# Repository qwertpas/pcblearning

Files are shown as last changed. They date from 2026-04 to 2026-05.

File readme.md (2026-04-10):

# pcblearning
A collection of PCB and firmware projects for learning PCB design. Projects are designed to have few components, cheap, yet rich in potential features.

## Using common libraries
1. After creating a new project in KiCad, copy the contents of `copy-into-your-project` into the same folder that contains your project's `.kicad_pcb` file.
2. Restart KiCad. When you place new components in the schematic or PCB editor, the `pcblearning` library should be available.

## minrc1
Tiny wheeled robot with two PM08 stepper motors, three microphones, and a buzzer. ESP32S3 supermini dev board allows for wireless control, USB-C battery charging, and running small neural networks. Microphones and buzzer may be useful for locating other robots, echolocation, and detecting surface properties (through vibration/noise from ground contact).
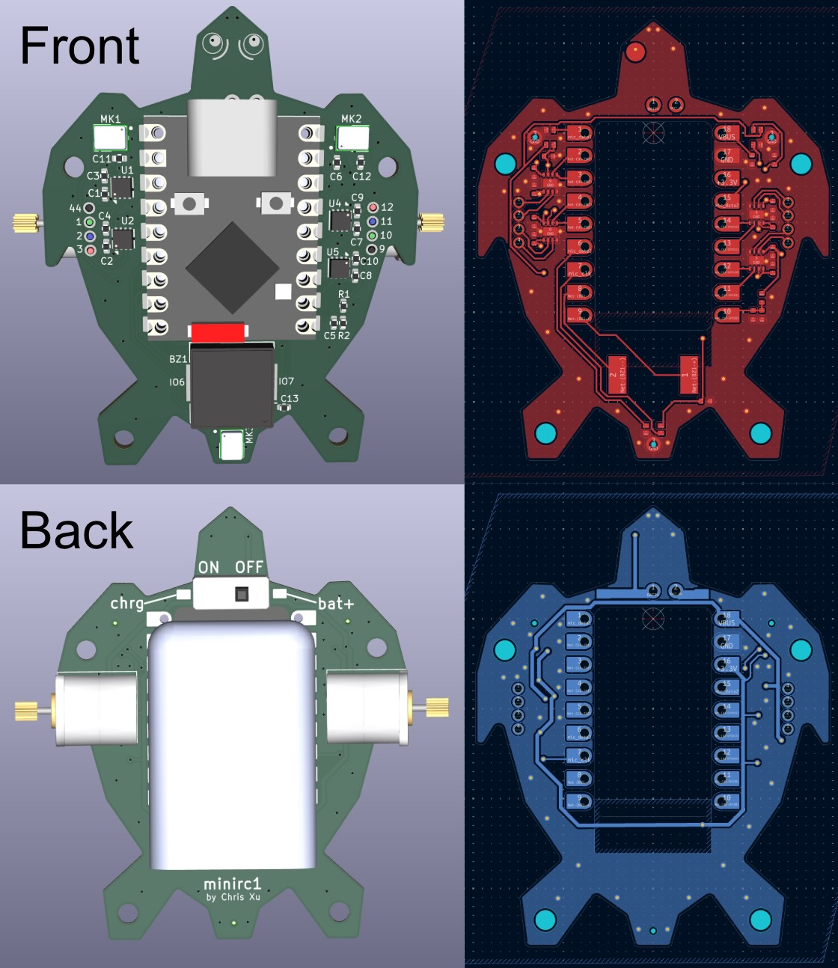
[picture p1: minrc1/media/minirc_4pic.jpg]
minrc1

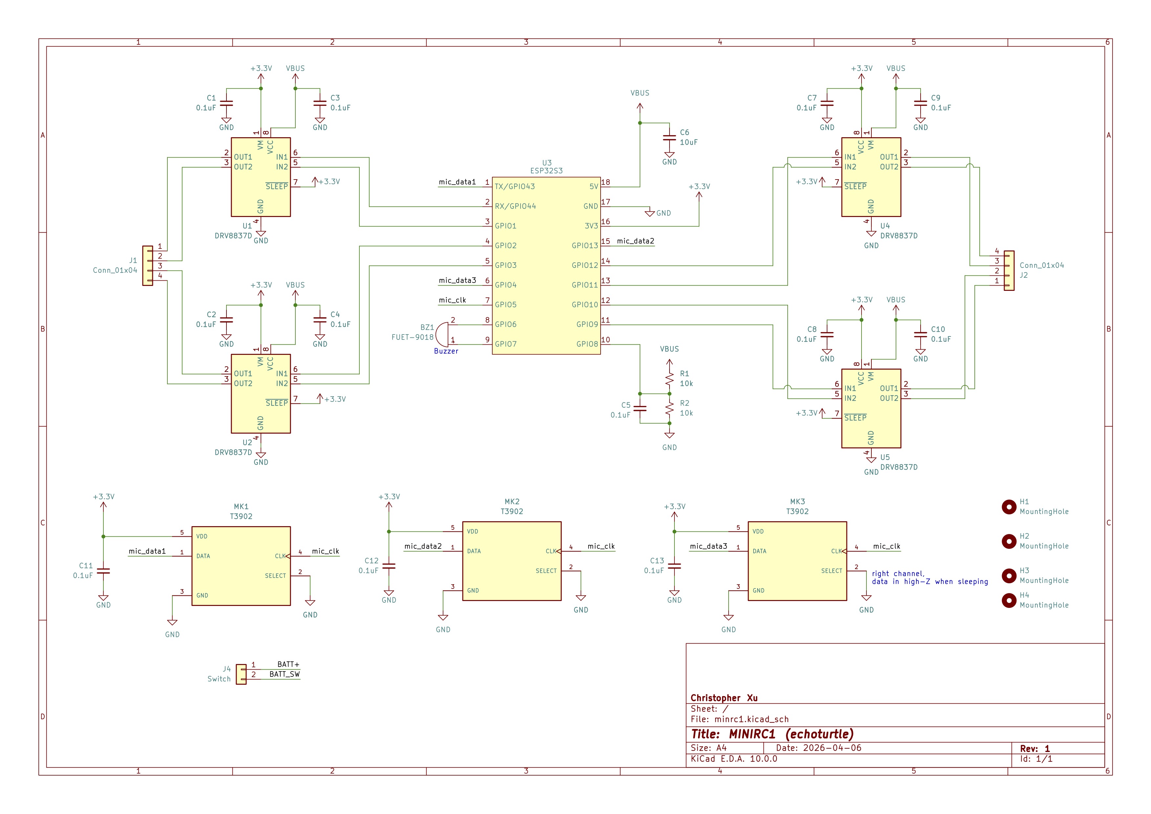
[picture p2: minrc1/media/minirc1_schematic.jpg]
schematic


## minrc-ref
Even more minimal than minrc1: just an ESP32S3-supermini, 4x DRV8837 motor drivers, 2x stepper motors, and resistor divider voltage sense. Intended as a reference design to be used as a starting point.

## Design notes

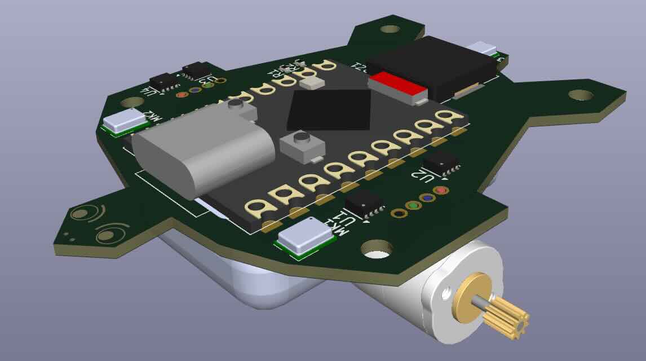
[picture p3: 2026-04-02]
minrc1/media/turtleside.jpg

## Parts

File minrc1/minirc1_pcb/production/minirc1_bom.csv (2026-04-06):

Designator | Footprint | Quantity | Value | LCSC Part #
BZ1 | Buzzer_CUI_CPT-9019S-SMT | 1 | FUET-9018
C1, C10, C11, C12, C13, C2, C3, C4, C5, C7, C8, C9 | 0402 | 12 | 0.1uF
C6 | 0402 | 1 | 10uF
J1, J2 | microstepper | 2 | Conn_01x04
J4 | PinHeader_1x02_P2.54mm_Vertical | 1 | Switch
MK1, MK2, MK3 | MIC_T3902 | 3 | T3902
R1, R2 | 0402 | 2 | 10k
U1, U2, U4, U5 | WSON-8-1EP_2x2mm_P0.5mm_EP0.9x1.6mm | 4 | DRV8837D | C39159
U3 | esp32s3-supermini | 1 | ESP32S3

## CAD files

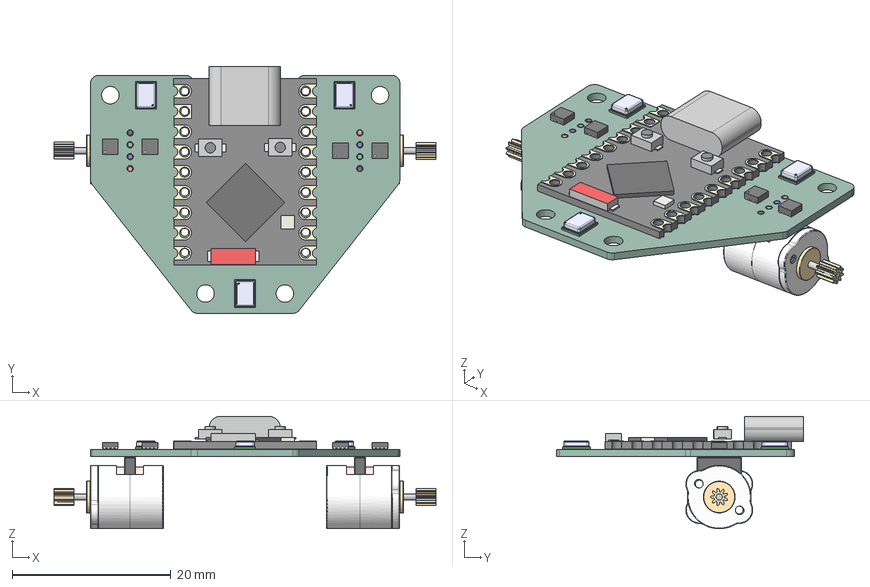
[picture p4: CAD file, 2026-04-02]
minrc1/minirc1_pcb/minirc1.step
48.2 x 31.1 x 14.2 mm
PCB
USB Type-C
SoC
BOOT
RESET
Antenna
LED
T3902 x 3
WSON-8-1EP_2x2mm_P0.5mm_EP0.9x1.6mm x 4
Spur Gear (9 teeth) x 2
Electrical Connector x 2
minrc1_PCB

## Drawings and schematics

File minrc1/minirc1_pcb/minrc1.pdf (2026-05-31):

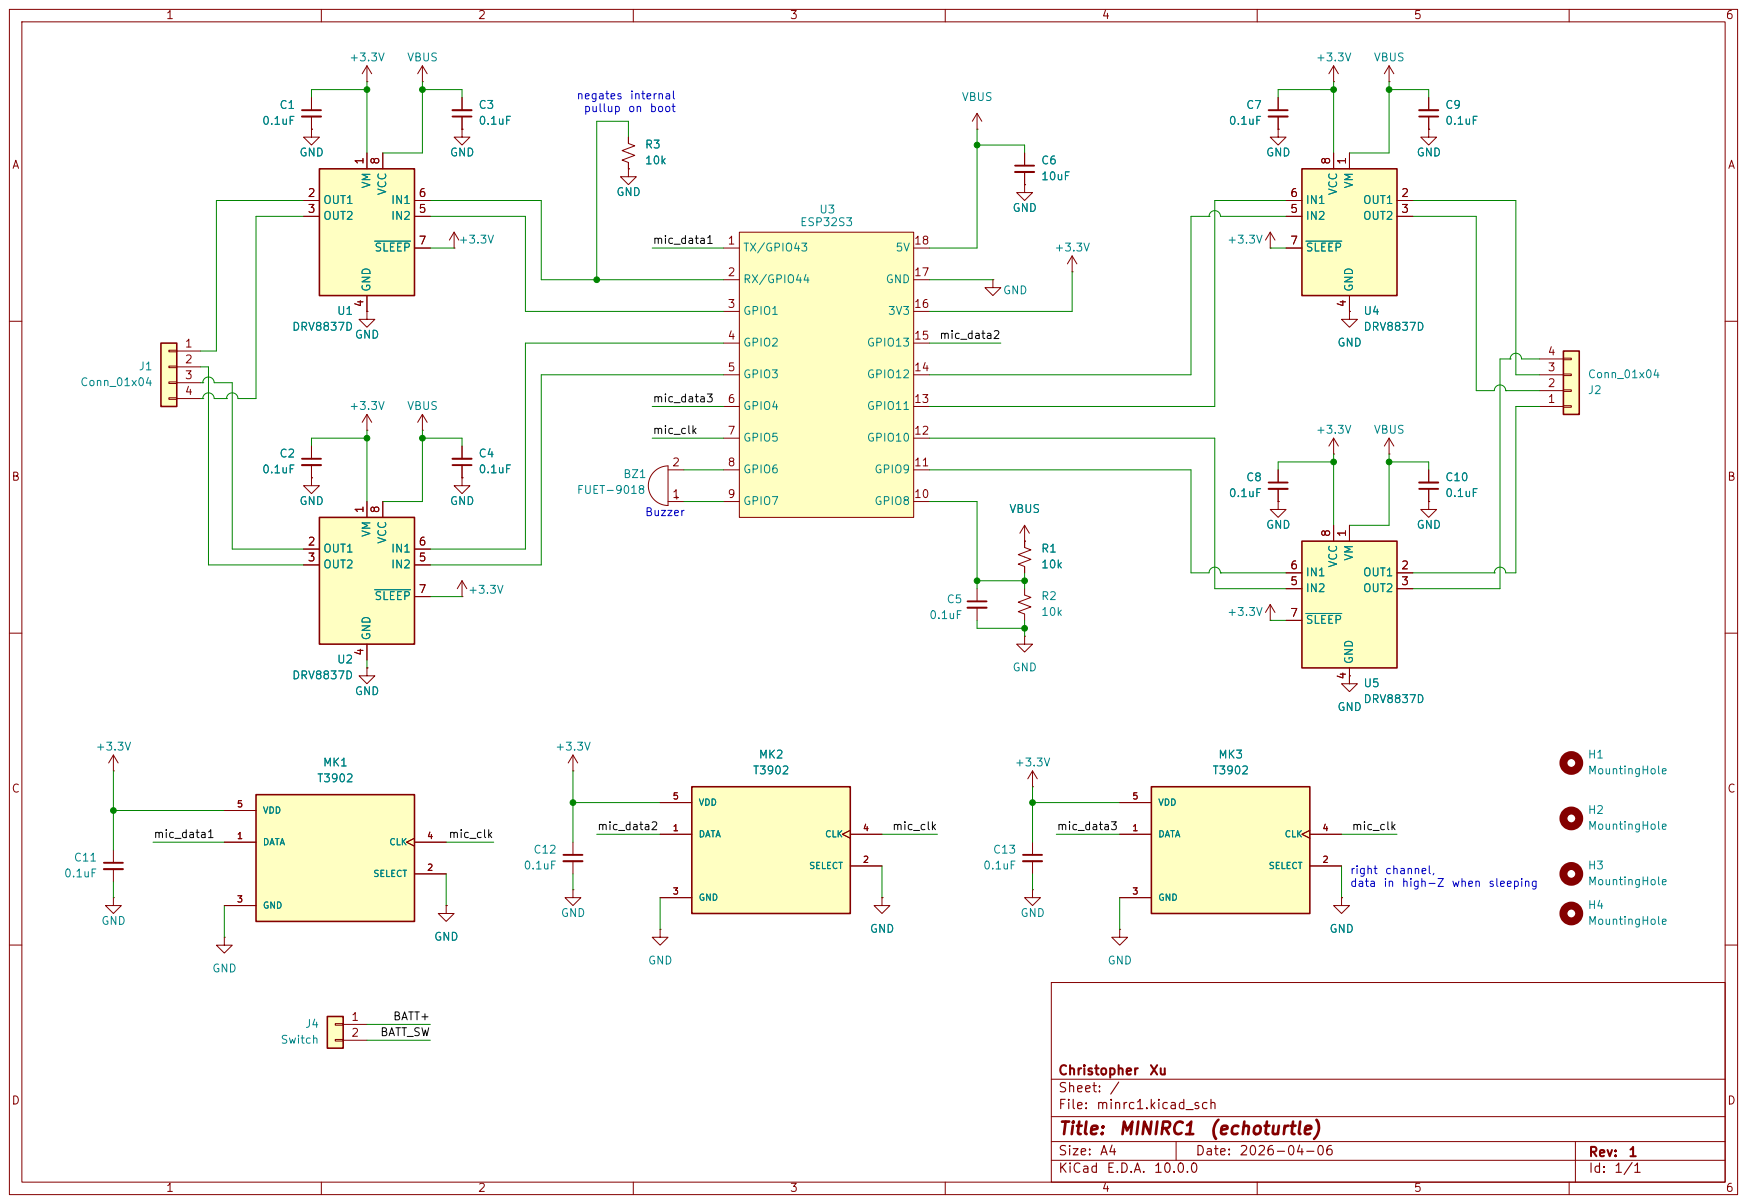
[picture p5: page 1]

right channel, data in high-Z when sleeping Buzzer negates internal

Size: A4 | Rev: 1

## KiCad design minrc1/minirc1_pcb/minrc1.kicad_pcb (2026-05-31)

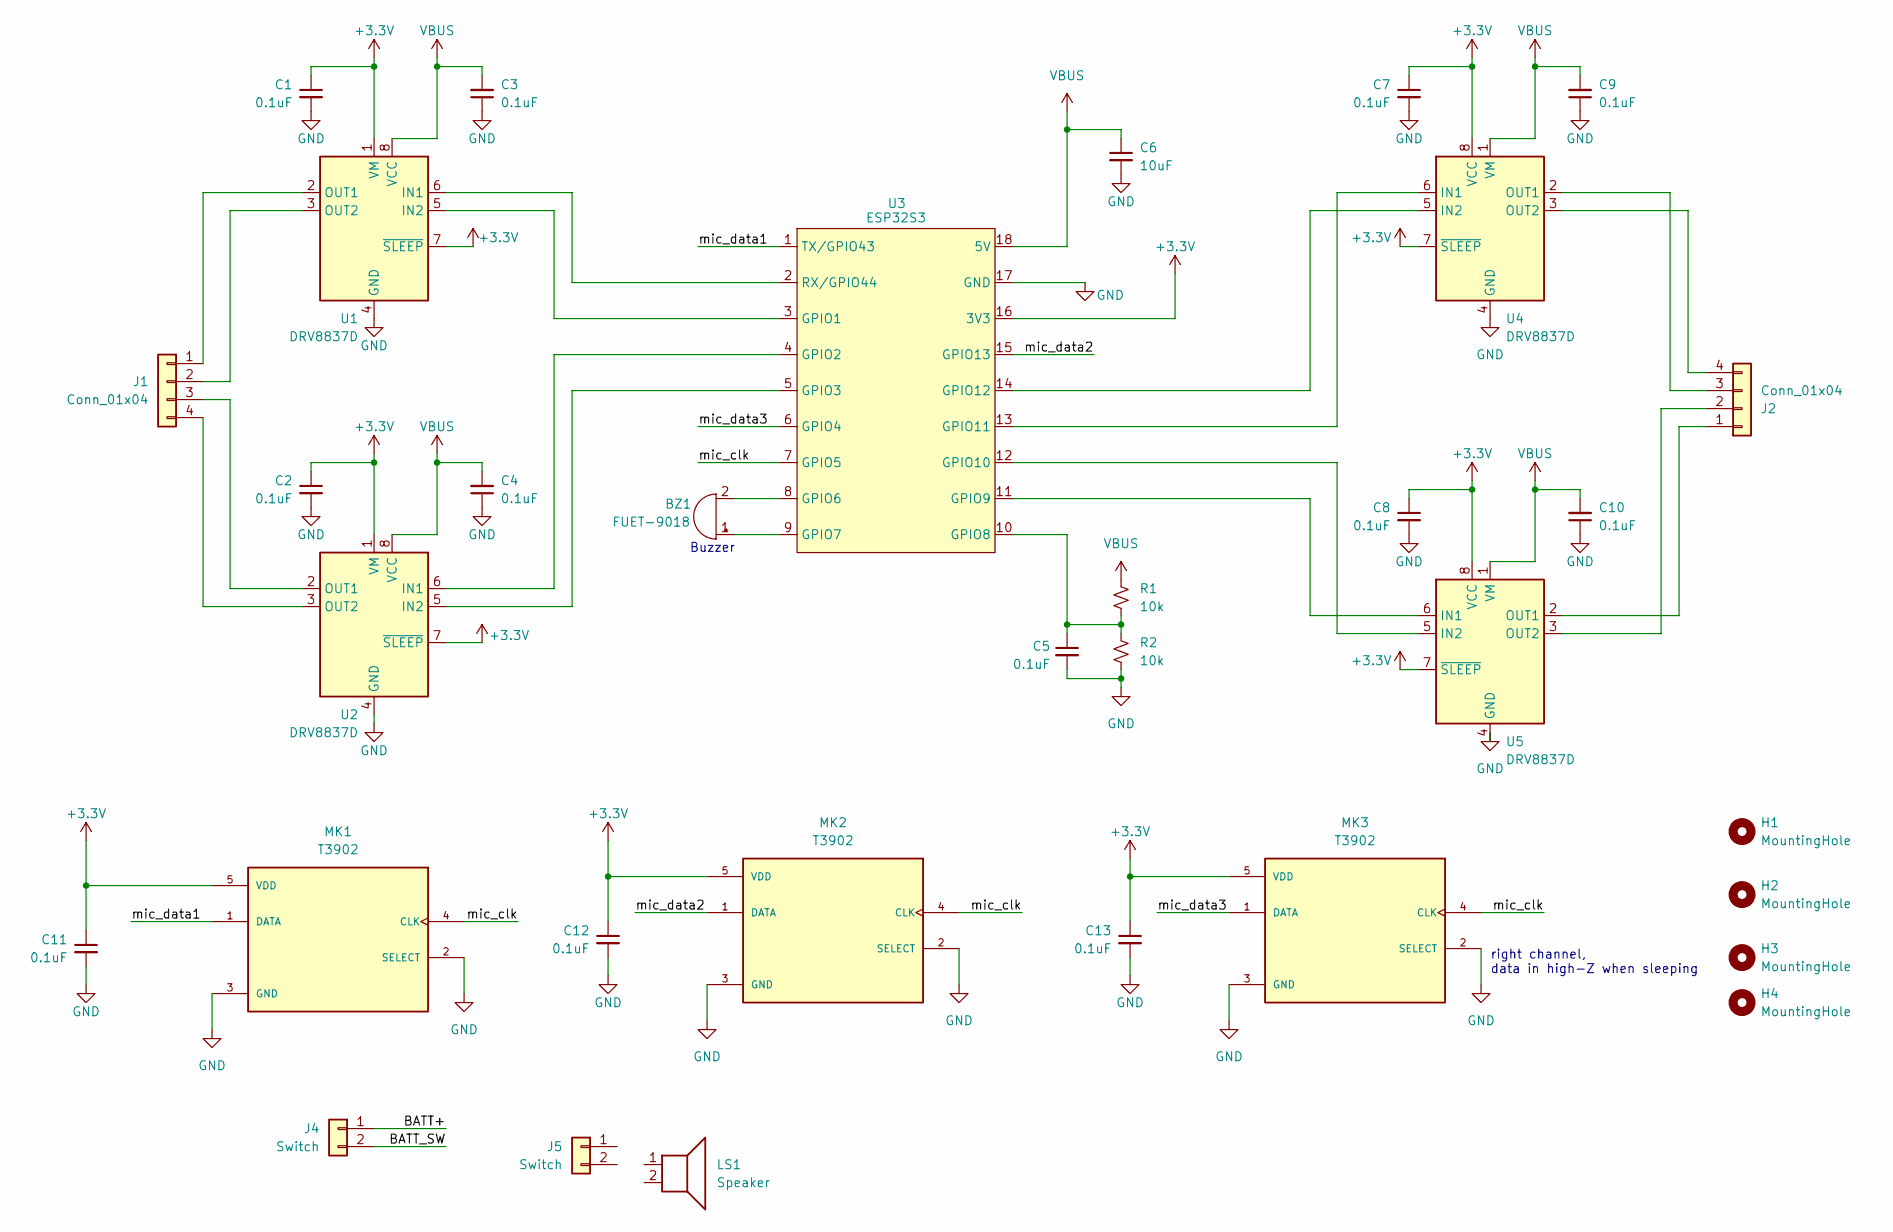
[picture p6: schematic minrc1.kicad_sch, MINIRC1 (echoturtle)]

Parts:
BZ1: FUET-9018; Buzzer_CUI_CPT-9019S-SMT
C1, C2, C3, C4, C5, C7, C8, C9, C10, C11, C12, C13: 0.1uF; C_0402_1005Metric
C6: 10uF; C_0402_1005Metric
H1, H2, H3, H4: MountingHole; MountingHole_2.2mm_M2
J1, J2: Conn_01x04; microstepper
J4, J5: Switch; PinHeader_1x02_P2.54mm_Vertical
LS1: Speaker; Speaker_CUI_CMR-1206S-67
MK1, MK2, MK3: T3902; MIC_T3902; PARTREV 1.0
R1, R2: 10k; R_0402_1005Metric
U1, U2, U4, U5: DRV8837D; WSON-8-1EP_2x2mm_P0.5mm_EP0.9x1.6mm; LCSC C39159
U3: ESP32S3; esp32s3-supermini

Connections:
+3.3V: C1.1, C2.1, C7.1, C8.1, C11.1, C12.1, C13.1, MK1.5 (VDD), MK2.5 (VDD), MK3.5 (VDD), U1.1 (VM), U1.7 (~SLEEP), U2.1 (VM), U2.7 (~SLEEP), U3.16 (3V3), U4.7 (~SLEEP), U4.8 (VCC), U5.7 (~SLEEP), U5.8 (VCC)
/BATT+: J4.1
/BATT_SW: J4.2
/mic_clk: MK1.4 (CLK), MK2.4 (CLK), MK3.4 (CLK), U3.7 (GPIO5)
/mic_data1: MK1.1 (DATA), U3.1 (TX/GPIO43)
/mic_data2: MK2.1 (DATA), U3.15 (GPIO13)
/mic_data3: MK3.1 (DATA), U3.6 (GPIO4)
GND: C1.2, C2.2, C3.1, C4.1, C5.2, C6.2, C7.2, C8.2, C9.1, C10.1, C11.2, C12.2, C13.2, MK1.2 (SELECT), MK1.3 (GND), MK2.2 (SELECT), MK2.3 (GND), MK3.2 (SELECT), MK3.3 (GND), R2.2, U1.4 (GND), U1.9 (GND), U2.4 (GND), U2.9 (GND), U3.17 (GND), U4.4 (GND), U4.9 (GND), U5.4 (GND), U5.9 (GND)
unnamed: BZ1.1 (+), U3.9 (GPIO7)
unnamed: BZ1.2 (-), U3.8 (GPIO6)
unnamed: J1.1, U1.2 (OUT1)
unnamed: J1.2, U1.3 (OUT2)
unnamed: J1.3, U2.2 (OUT1)
unnamed: J1.4, U2.3 (OUT2)
unnamed: J2.1, U5.2 (OUT1)
unnamed: J2.2, U5.3 (OUT2)
unnamed: J2.3, U4.2 (OUT1)
unnamed: J2.4, U4.3 (OUT2)
unnamed: U1.6 (IN1), U3.2 (RX/GPIO44)
unnamed: U1.5 (IN2), U3.3 (GPIO1)
unnamed: U2.6 (IN1), U3.4 (GPIO2)
unnamed: U2.5 (IN2), U3.5 (GPIO3)
unnamed: C5.1, R1.2, R2.1, U3.10 (GPIO8)
unnamed: U3.11 (GPIO9), U5.6 (IN1)
unnamed: U3.12 (GPIO10), U5.5 (IN2)
unnamed: U3.13 (GPIO11), U4.6 (IN1)
unnamed: U3.14 (GPIO12), U4.5 (IN2)
VBUS: C3.2, C4.2, C6.1, C9.2, C10.2, R1.1, U1.8 (VCC), U2.8 (VCC), U3.18 (5V), U4.1 (VM), U5.1 (VM)

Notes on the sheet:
right channel, data in high-Z when sleeping
Buzzer

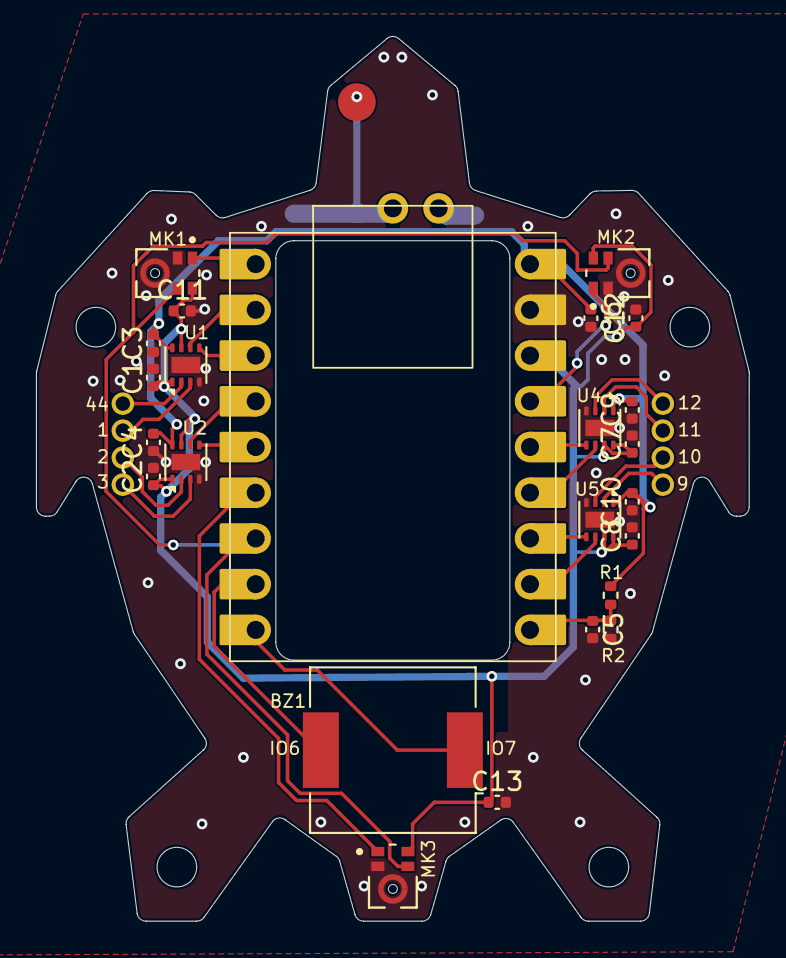
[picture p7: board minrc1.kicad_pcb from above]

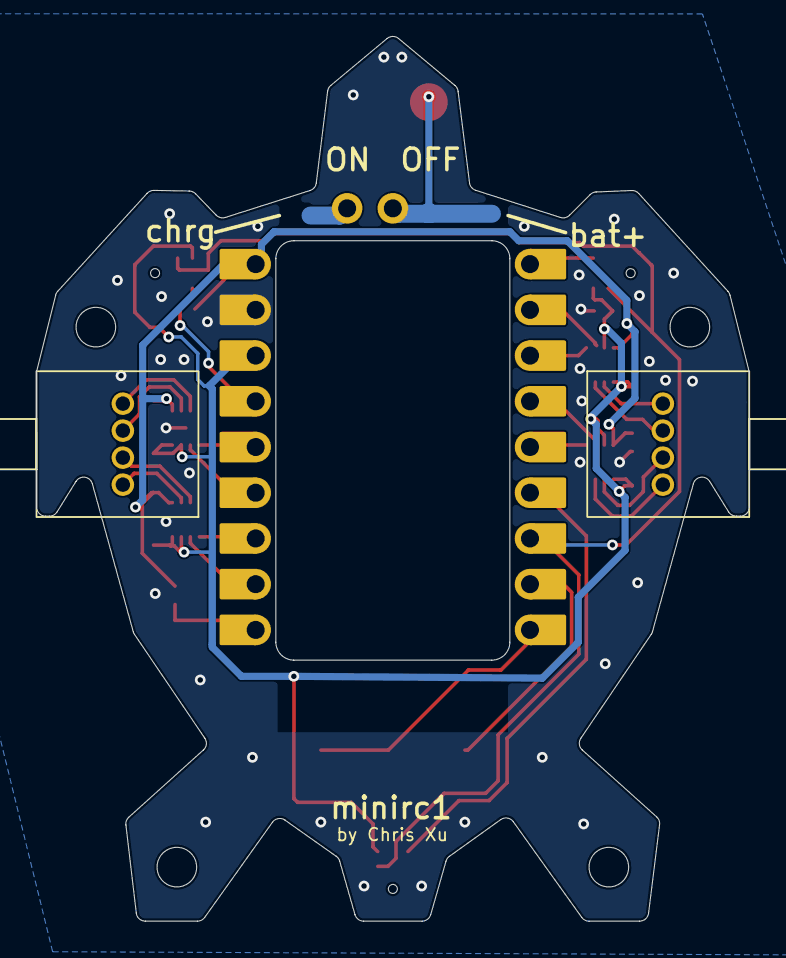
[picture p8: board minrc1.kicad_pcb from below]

Board: 2 copper layers, 39.6 x 49.1 mm, 31 parts (3 on the bottom side), 26 nets.

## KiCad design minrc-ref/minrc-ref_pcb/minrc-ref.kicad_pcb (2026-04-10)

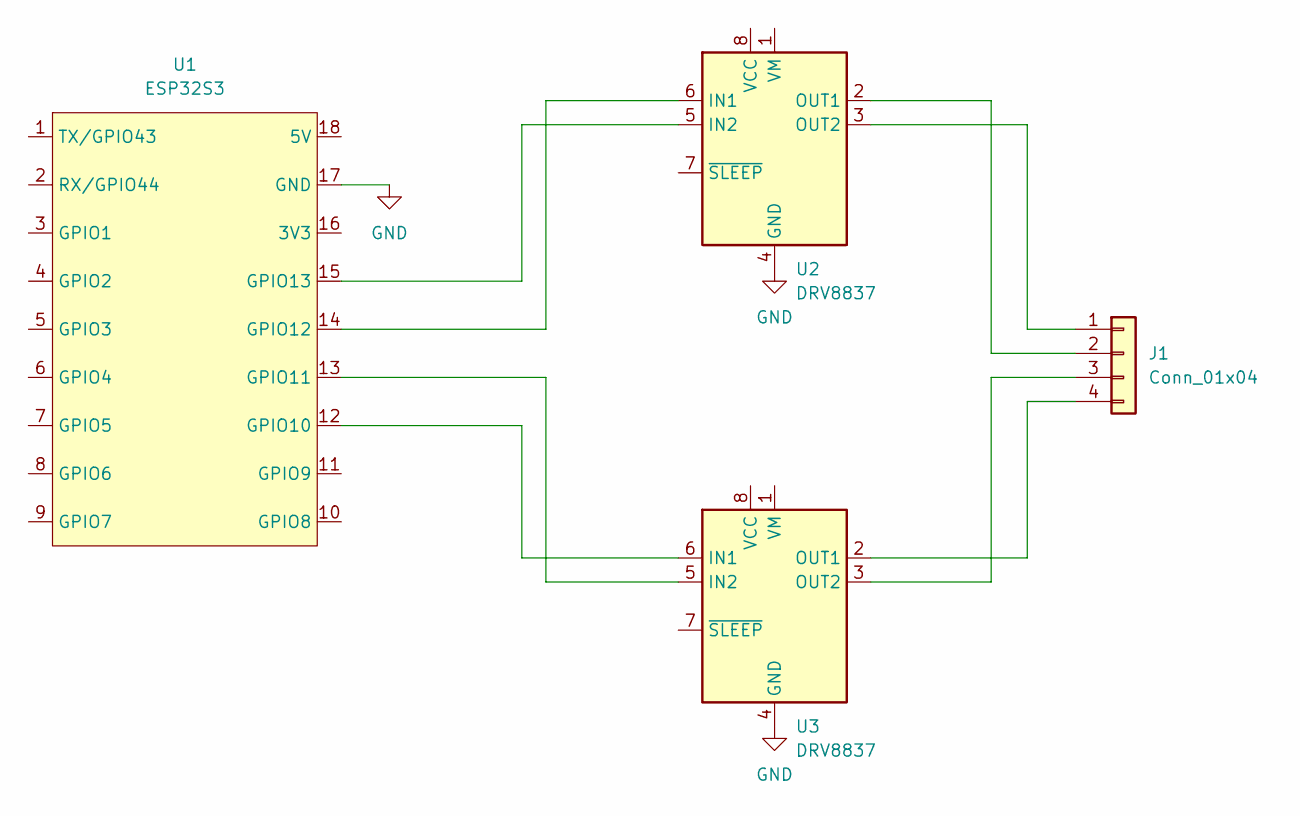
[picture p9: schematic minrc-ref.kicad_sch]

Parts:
J1: Conn_01x04; PM08_stepper_motor
U1: ESP32S3; ESP32-S3-SUPERMINI
U2, U3: DRV8837; WSON-8-1EP_2x2mm_P0.5mm_EP0.9x1.6mm

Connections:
GND: U1.17 (GND), U2.4 (GND), U2.9 (GND), U3.4 (GND), U3.9 (GND)
unnamed: J1.1, U2.3 (OUT2)
unnamed: J1.2, U2.2 (OUT1)
unnamed: J1.3, U3.3 (OUT2)
unnamed: J1.4, U3.2 (OUT1)
unnamed: U1.12 (GPIO10), U3.6 (IN1)
unnamed: U1.13 (GPIO11), U3.5 (IN2)
unnamed: U1.14 (GPIO12), U2.6 (IN1)
unnamed: U1.15 (GPIO13), U2.5 (IN2)

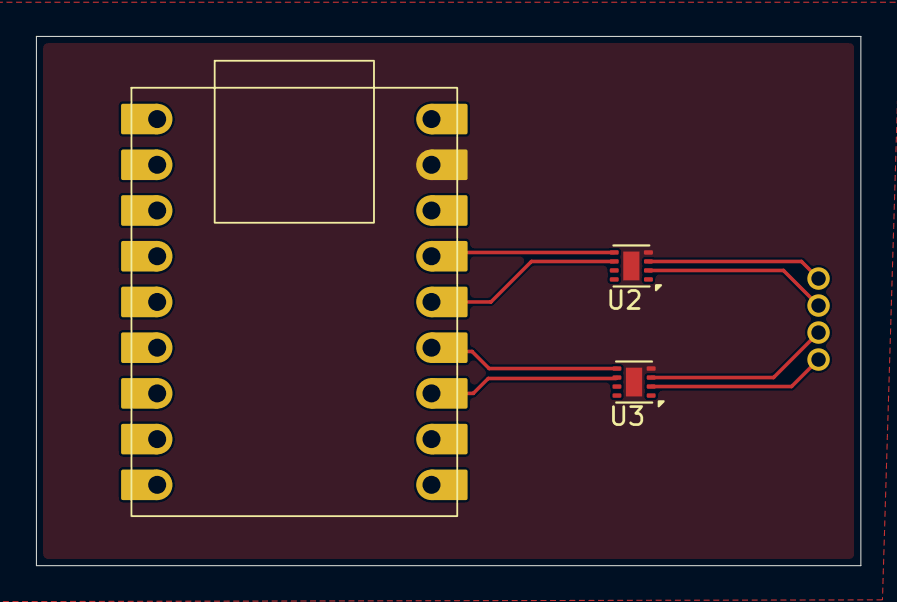
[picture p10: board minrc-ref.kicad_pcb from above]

Board: 2 copper layers, 45.8 x 29.4 mm, 4 parts (1 on the bottom side), 9 nets.

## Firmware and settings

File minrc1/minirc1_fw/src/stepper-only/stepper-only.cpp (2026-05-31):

#include <Arduino.h>
#include <Adafruit_NeoPixel.h>
#include <Preferences.h>
#include <BLEDevice.h>
#include <BLEServer.h>
#include <BLEUtils.h>
#include <BLE2902.h>
#include <esp32-hal-matrix.h>

#include <cmath>
#include <string>

struct Coil {
  uint8_t pinPos;
  uint8_t pinNeg;
  uint8_t channel;
};

struct Motor {
  Coil coilA;
  Coil coilB;
};

struct MotorState {
  uint8_t stepIndex;
  uint32_t lastStepUs;
  float stepHz;
};

constexpr Motor kMotors[2] = {
  {{44, 1, 0}, {2, 3, 1}},
  {{9, 10, 2}, {11, 12, 3}},
};

constexpr uint8_t kPwmBits = 8;
constexpr uint16_t kPwmMax = (1u << kPwmBits) - 1;
constexpr int8_t kPhases[][2] = {
  {1, 1},
  {-1, 1},
  {-1, -1},
  {1, -1},
};
constexpr uint8_t kPhaseCount = sizeof(kPhases) / sizeof(kPhases[0]);

constexpr uint16_t kStepsPerHueCycle = 20;
constexpr uint8_t kWs2812Pin = 48;
constexpr uint16_t kPixelCount = 1;
constexpr uint8_t kVbusSensePin = 8;
constexpr uint8_t kVbusSamples = 8;
constexpr float kVbusDividerScale = 2.0f;
constexpr uint8_t kBuzzerPinPos = 7;
constexpr uint8_t kBuzzerPinNeg = 6;
constexpr uint8_t kBuzzerChannel = 4;
constexpr uint32_t kDefaultBuzzerFreqHz = 4000;
constexpr uint32_t kBuzzerOnMs = 120;

constexpr char kBleDeviceName[] = "MinRC1-Stepper";
constexpr char kUartServiceUuid[] = "6E400001-B5A3-F393-E0A9-E50E24DCCA9E";
constexpr char kUartRxUuid[] = "6E400002-B5A3-F393-E0A9-E50E24DCCA9E";
constexpr char kUartTxUuid[] = "6E400003-B5A3-F393-E0A9-E50E24DCCA9E";

constexpr char kPrefsNamespace[] = "stepper";
constexpr char kPrefsDuty[] = "duty";
constexpr char kPrefsFreqKhz[] = "fkhz";
constexpr char kPrefsPeriodMs[] = "pms";
constexpr char kPrefsRun[] = "run";
constexpr char kPrefsOrder[] = "order";

Adafruit_NeoPixel pixels(kPixelCount, kWs2812Pin, NEO_GRB + NEO_KHZ800);

uint32_t stepCount = 0;
float pwmDutyPercent = 80.0f;
float pwmFreqKhz = 20.0f;
float stepPeriodMs = 10.0f;
String command;
char phaseOrder[5] = "0123";
MotorState motorStates[2] = {
  {0, 0, 0.0f},
  {0, 0, 0.0f},
};

BLEServer* bleServer = nullptr;
BLECharacteristic* bleTxCharacteristic = nullptr;
bool bleConnected = false;
bool bleOldConnected = false;
bool buzzerOn = false;
uint32_t buzzerOffMs = 0;
uint32_t buzzerFreqHz = kDefaultBuzzerFreqHz;

portMUX_TYPE bleCmdMux = portMUX_INITIALIZER_UNLOCKED;
String bleIncoming;

uint32_t pwmFreqHz() {
  return static_cast<uint32_t>(pwmFreqKhz * 1000.0f + 0.5f);
}

uint32_t stepPeriodUs() {
  return static_cast<uint32_t>(stepPeriodMs * 1000.0f + 0.5f);
}

uint32_t pwmDutyValue() {
  return static_cast<uint32_t>(pwmDutyPercent * kPwmMax / 100.0f + 0.5f);
}

float defaultStepHz() {
  if (stepPeriodMs <= 0.0f) {
    return 0.0f;
  }
  return 1000.0f / stepPeriodMs;
}

bool anyMotorRunning() {
  return motorStates[0].stepHz != 0.0f || motorStates[1].stepHz != 0.0f;
}

void bleNotify(const String& s) {
  if (bleTxCharacteristic != nullptr && bleConnected) {
    bleTxCharacteristic->setValue(s.c_str());
    bleTxCharacteristic->notify();
  }
}

void replyln(const String& line) {
  Serial.println(line);
  bleNotify(line + "\n");
}

void driveCoil(const Coil& coil, int8_t state) {
  ledcDetachPin(coil.pinPos);
  ledcDetachPin(coil.pinNeg);
  digitalWrite(coil.pinPos, LOW);
  digitalWrite(coil.pinNeg, LOW);

  if (state == 0 || pwmDutyPercent <= 0.0f) {
    return;
  }

  if (pwmDutyPercent >= 100.0f) {
    digitalWrite(state > 0 ? coil.pinPos : coil.pinNeg, HIGH);
    return;
  }

  const uint8_t activePin = state > 0 ? coil.pinPos : coil.pinNeg;
  ledcAttachPin(activePin, coil.channel);
  ledcWrite(coil.channel, pwmDutyValue());
}

void setMotorPhase(uint8_t motorIndex, uint8_t nextPhase) {
  const Motor& motor = kMotors[motorIndex];
  driveCoil(motor.coilA, kPhases[nextPhase][0]);
  driveCoil(motor.coilB, kPhases[nextPhase][1]);
}

uint8_t phaseIndexForStep(uint8_t step) {
  return static_cast<uint8_t>(phaseOrder[step % kPhaseCount] - '0');
}

bool parsePhaseOrder(const String& text, char out[5]) {
  if (text.length() != kPhaseCount) {
    return false;
  }

  bool seen[kPhaseCount] = {false, false, false, false};
  for (uint8_t i = 0; i < kPhaseCount; ++i) {
    const char c = text[i];
    if (c < '0' || c >= ('0' + kPhaseCount)) {
      return false;
    }
    const uint8_t value = static_cast<uint8_t>(c - '0');
    if (seen[value]) {
      return false;
    }
    seen[value] = true;
    out[i] = c;
  }
  out[kPhaseCount] = '\0';
  return true;
}

void stopMotor(uint8_t motorIndex) {
  const Motor& motor = kMotors[motorIndex];
  driveCoil(motor.coilA, 0);
  driveCoil(motor.coilB, 0);
}

void stopMotors() {
  for (uint8_t i = 0; i < 2; ++i) {
    motorStates[i].stepHz = 0.0f;
    stopMotor(i);
  }
}

void setupMotorPinsLow() {
  for (const Motor& motor : kMotors) {
    for (const Coil& coil : {motor.coilA, motor.coilB}) {
      pinMode(coil.pinPos, OUTPUT);
      pinMode(coil.pinNeg, OUTPUT);
      digitalWrite(coil.pinPos, LOW);
      digitalWrite(coil.pinNeg, LOW);
    }
  }
}

void updateRgbForStep() {
  const uint32_t s = (stepCount - 1u) % kStepsPerHueCycle;
  const uint16_t hueNow = static_cast<uint16_t>((s * 65536u) / kStepsPerHueCycle);
  pixels.setPixelColor(0, pixels.gamma32(pixels.ColorHSV(hueNow, 255, 255)));
  pixels.show();
}

void setupBuzzer() {
  ledcSetup(kBuzzerChannel, buzzerFreqHz, kPwmBits);
  ledcAttachPin(kBuzzerPinPos, kBuzzerChannel);
  pinMode(kBuzzerPinNeg, OUTPUT);
  ledcWrite(kBuzzerChannel, 0);
  digitalWrite(kBuzzerPinNeg, LOW);
}

void stopBuzzer() {
  buzzerOn = false;
  ledcWrite(kBuzzerChannel, 0);
  pinMatrixOutDetach(kBuzzerPinNeg, false, false);
  digitalWrite(kBuzzerPinNeg, LOW);
}

void beepBuzzer(uint32_t durationMs = kBuzzerOnMs) {
  ledcSetup(kBuzzerChannel, buzzerFreqHz, kPwmBits);
  buzzerOn = true;
  buzzerOffMs = millis() + durationMs;
  pinMatrixOutAttach(kBuzzerPinNeg, LEDC_LS_SIG_OUT0_IDX + kBuzzerChannel, true, false);
  ledcWrite(kBuzzerChannel, kPwmMax / 2);
}

void setBuzzerFreq(uint32_t nextFreqHz) {
  buzzerFreqHz = nextFreqHz;
  ledcSetup(kBuzzerChannel, buzzerFreqHz, kPwmBits);
  if (buzzerOn) {
    ledcWrite(kBuzzerChannel, kPwmMax / 2);
  }
}

void updateBuzzer() {
  if (!buzzerOn) {
    return;
  }
  if (static_cast<int32_t>(millis() - buzzerOffMs) >= 0) {
    stopBuzzer();
  }
}

float readVbusVolts() {
  uint32_t sumMv = 0;
  for (uint8_t i = 0; i < kVbusSamples; ++i) {
    sumMv += static_cast<uint32_t>(analogReadMilliVolts(kVbusSensePin));
  }
  const float pinVolts = static_cast<float>(sumMv) / static_cast<float>(kVbusSamples) / 1000.0f;
  return pinVolts * kVbusDividerScale;
}

void refreshMotorOutputs() {
  for (uint8_t i = 0; i < 2; ++i) {
    if (motorStates[i].stepHz == 0.0f) {
      stopMotor(i);
      continue;
    }
    setMotorPhase(i, phaseIndexForStep(motorStates[i].stepIndex));
  }
}

void printVbus() {
  replyln("vbus_v=" + String(readVbusVolts(), 3));
}

void loadPrefs() {
  Preferences prefs;
  if (!prefs.begin(kPrefsNamespace, true)) {
    return;
  }

  const float duty = prefs.getFloat(kPrefsDuty, pwmDutyPercent);
  const float freq = prefs.getFloat(kPrefsFreqKhz, pwmFreqKhz);
  const float period = prefs.getFloat(kPrefsPeriodMs, stepPeriodMs);
  const String order = prefs.isKey(kPrefsOrder) ? prefs.getString(kPrefsOrder, phaseOrder) : String(phaseOrder);
  prefs.end();

  if (duty >= 0.0f && duty <= 100.0f) {
    pwmDutyPercent = duty;
  }
  if (freq > 0.0f) {
    pwmFreqKhz = freq;
  }
  if (period > 0.0f) {
    stepPeriodMs = period;
  }
  char loadedOrder[5];
  if (parsePhaseOrder(order, loadedOrder)) {
    memcpy(phaseOrder, loadedOrder, sizeof(phaseOrder));
  }
}

void savePrefs() {
  Preferences prefs;
  if (!prefs.begin(kPrefsNamespace, false)) {
    return;
  }
  prefs.putFloat(kPrefsDuty, pwmDutyPercent);
  prefs.putFloat(kPrefsFreqKhz, pwmFreqKhz);
  prefs.putFloat(kPrefsPeriodMs, stepPeriodMs);
  prefs.putBool(kPrefsRun, anyMotorRunning());
  prefs.putString(kPrefsOrder, phaseOrder);
  prefs.end();
}

void setupPwm() {
  for (const Motor& motor : kMotors) {
    for (const Coil& coil : {motor.coilA, motor.coilB}) {
      pinMode(coil.pinPos, OUTPUT);
      pinMode(coil.pinNeg, OUTPUT);
      digitalWrite(coil.pinPos, LOW);
      digitalWrite(coil.pinNeg, LOW);
      ledcSetup(coil.channel, pwmFreqHz(), kPwmBits);
      ledcWrite(coil.channel, 0);
    }
  }
}

void printState() {
  const String line = "duty_pct=" + String(pwmDutyPercent, 2) +
                      " freq_khz=" + String(pwmFreqKhz, 3) +
                      " period_ms=" + String(stepPeriodMs, 3) +
                      " run=" + String(anyMotorRunning() ? 1 : 0) +
                      " left_hz=" + String(motorStates[0].stepHz, 3) +
                      " right_hz=" + String(motorStates[1].stepHz, 3) +
                      " beep_hz=" + String(buzzerFreqHz) +
                      " vbus_v=" + String(readVbusVolts(), 3) +
                      " order=" + String(phaseOrder);
  replyln(line);
}

bool parseDriveValue(const String& text, float& out) {
  if (text.length() == 0) {
    return false;
  }
  char* end = nullptr;
  const float value = strtof(text.c_str(), &end);
  if (end == nullptr || *end != '\0' || !std::isfinite(value)) {
    return false;
  }
  out = value;
  return true;
}

bool parseDrivePair(const String& text, float& leftHz, float& rightHz) {
  const int comma = text.indexOf(',');
  if (comma <= 0 || comma >= static_cast<int>(text.length()) - 1) {
    return false;
  }
  return parseDriveValue(text.substring(0, comma), leftHz) &&
         parseDriveValue(text.substring(comma + 1), rightHz);
}

void setDrive(float leftHz, float rightHz) {
  const float nextHz[2] = {leftHz, rightHz};
  const uint32_t nowUs = micros();

  for (uint8_t i = 0; i < 2; ++i) {
    const bool wasStopped = motorStates[i].stepHz == 0.0f;
    motorStates[i].stepHz = nextHz[i];
    if (motorStates[i].stepHz == 0.0f) {
      stopMotor(i);
      continue;
    }
    if (wasStopped) {
      motorStates[i].lastStepUs = nowUs;
      setMotorPhase(i, phaseIndexForStep(motorStates[i].stepIndex));
    }
  }
}

void applyCommand() {
  if (command.length() == 0) {
    command = "";
    return;
  }

  const char type = command[0];
  const String valueText = command.substring(1);

  if (type == 'b' && command.length() == 1) {
    printVbus();
    command = "";
    return;
  }

  if (type == 'q' && command.length() == 1) {
    printState();
    command = "";
    return;
  }

  if (type == 'x' && command.length() == 1) {
    beepBuzzer();
    command = "";
    return;
  }

  if (command.length() < 2) {
    command = "";
    return;
  }

  const float value = valueText.toFloat();

  if (type == 'd') {
    if (value < 0.0f || value > 100.0f) {
      replyln("bad duty");
    } else {
      pwmDutyPercent = value;
      refreshMotorOutputs();
      savePrefs();
      printState();
    }
  } else if (type == 'f') {
    if (value <= 0.0f) {
      replyln("bad freq");
    } else {
      pwmFreqKhz = value;
      setupPwm();
      refreshMotorOutputs();
      savePrefs();
      printState();
    }
  } else if (type == 'p') {
    if (value <= 0.0f) {
      replyln("bad period");
    } else {
      stepPeriodMs = value;
      savePrefs();
      printState();
    }
  } else if (type == 'r') {
    if (value < 0.5f) {
      stepCount = 0;
      setDrive(0.0f, 0.0f);
    } else {
      const float stepHz = defaultStepHz();
      setDrive(stepHz, stepHz);
    }
    savePrefs();
    printState();
  } else if (type == 'v') {
    float leftHz = 0.0f;
    float rightHz = 0.0f;
    if (!parseDrivePair(valueText, leftHz, rightHz)) {
      replyln("bad drive");
    } else {
      setDrive(leftHz, rightHz);
      printState();
    }
  } else if (type == 'o') {
    char nextOrder[5];
    if (!parsePhaseOrder(valueText, nextOrder)) {
      replyln("bad order");
    } else {
      memcpy(phaseOrder, nextOrder, sizeof(phaseOrder));
      refreshMotorOutputs();
      savePrefs();
      printState();
    }
  } else if (type == 'z') {
    const uint32_t nextFreqHz = static_cast<uint32_t>(value + 0.5f);
    if (nextFreqHz < 100 || nextFreqHz > 20000) {
      replyln("bad beep");
    } else {
      setBuzzerFreq(nextFreqHz);
      printState();
    }
  } else {
    replyln("bad cmd");
  }

  command = "";
}

void drainBleIncoming() {
  String chunk;
  portENTER_CRITICAL(&bleCmdMux);
  if (bleIncoming.length() > 0) {
    chunk = bleIncoming;
    bleIncoming = "";
  }
  portEXIT_CRITICAL(&bleCmdMux);

  for (unsigned i = 0; i < chunk.length(); ++i) {
    const char c = chunk[i];
    if (c == '\n' || c == '\r') {
      applyCommand();
    } else {
      command += c;
    }
  }
}

void readSerialCommands() {
  while (Serial.available() > 0) {
    const char c = static_cast<char>(Serial.read());
    if (c == '\n' || c == '\r') {
      applyCommand();
    } else {
      command += c;
    }
  }
}

class BleServerCallbacks : public BLEServerCallbacks {
  void onConnect(BLEServer* /* server */) override { bleConnected = true; }

  void onDisconnect(BLEServer* server) override {
    bleConnected = false;
    server->getAdvertising()->start();
  }
};

class BleRxCallbacks : public BLECharacteristicCallbacks {
  void onWrite(BLECharacteristic* characteristic) override {
    const std::string value = characteristic->getValue();
    if (value.empty()) {
      return;
    }
    portENTER_CRITICAL(&bleCmdMux);
    for (char c : value) {
      bleIncoming += c;
    }
    portEXIT_CRITICAL(&bleCmdMux);
  }
};

void setupBle() {
  BLEDevice::init(kBleDeviceName);
  bleServer = BLEDevice::createServer();
  bleServer->setCallbacks(new BleServerCallbacks());

  BLEService* service = bleServer->createService(kUartServiceUuid);
  BLECharacteristic* rxChar = service->createCharacteristic(
    kUartRxUuid,
    BLECharacteristic::PROPERTY_WRITE | BLECharacteristic::PROPERTY_WRITE_NR);
  rxChar->setCallbacks(new BleRxCallbacks());

  bleTxCharacteristic = service->createCharacteristic(
    kUartTxUuid,
    BLECharacteristic::PROPERTY_NOTIFY);
  bleTxCharacteristic->addDescriptor(new BLE2902());

  service->start();

  BLEAdvertising* adv = BLEDevice::getAdvertising();
  adv->addServiceUUID(kUartServiceUuid);
  adv->setScanResponse(true);
  adv->setMinPreferred(0x06);
  adv->setMinPreferred(0x12);
  BLEDevice::startAdvertising();
}

void setup() {
  setupMotorPinsLow();
  analogSetPinAttenuation(kVbusSensePin, ADC_11db);
  Serial.begin(115200);
  delay(100);

  pixels.begin();
  pixels.setBrightness(64);
  pixels.setPixelColor(0, pixels.gamma32(pixels.ColorHSV(0, 255, 255)));
  pixels.show();

  loadPrefs();
  setupPwm();
  setupBuzzer();
  stopBuzzer();
  stopMotors();
  printState();
  setupBle();
  replyln("BLE ready; commands: v<left_hz,right_hz> d<duty_pct> b(vbus) q(state) x(beep) z<beep_hz> o0123/o0321");
}

void loop() {
  readSerialCommands();
  drainBleIncoming();
  updateBuzzer();

  if (!bleConnected && bleOldConnected) {
    delay(500);
    bleServer->startAdvertising();
    bleOldConnected = bleConnected;
  }
  if (bleConnected && !bleOldConnected) {
    bleOldConnected = bleConnected;
  }

  const uint32_t nowUs = micros();
  for (uint8_t i = 0; i < 2; ++i) {
    const float stepHz = std::fabs(motorStates[i].stepHz);
    if (stepHz <= 0.0f) {
      continue;
    }

    const uint32_t periodUs = static_cast<uint32_t>(1000000.0f / stepHz);
    if (periodUs == 0 || nowUs - motorStates[i].lastStepUs < periodUs) {
      continue;
    }

    motorStates[i].lastStepUs = nowUs;
    setMotorPhase(i, phaseIndexForStep(motorStates[i].stepIndex));
    if (motorStates[i].stepHz > 0.0f) {
      motorStates[i].stepIndex = (motorStates[i].stepIndex + 1u) % kPhaseCount;
    } else {
      motorStates[i].stepIndex = (motorStates[i].stepIndex + kPhaseCount - 1u) % kPhaseCount;
    }
    ++stepCount;
    updateRgbForStep();
  }
}

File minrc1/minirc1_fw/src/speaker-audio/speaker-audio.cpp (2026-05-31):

#include <Arduino.h>
#include <LittleFS.h>
#include "esp_heap_caps.h"

constexpr int AMP_ENABLE_PIN = 5;
constexpr int AMP_INPUT_NODE_PIN = 6;
constexpr int AUDIO_PIN = 7;

constexpr int SAMPLE_RATE = 22050;
constexpr int PWM_FREQ = 78125;
constexpr int PWM_BITS = 8;
constexpr int PWM_CHANNEL = 0;
constexpr int TIMER_DIVIDER = 8;
constexpr int TIMER_TICKS = 80000000 / TIMER_DIVIDER / SAMPLE_RATE;
constexpr int ACTUAL_SAMPLE_RATE = 80000000 / TIMER_DIVIDER / TIMER_TICKS;

hw_timer_t *audioTimer = nullptr;
portMUX_TYPE audioMux = portMUX_INITIALIZER_UNLOCKED;

uint8_t *audioData = nullptr;
volatile uint32_t activeLength = 0;
volatile uint32_t activeIndex = 0;
volatile bool playbackDone = false;
volatile uint32_t sampleCount = 0;
volatile uint32_t underruns = 0;
volatile uint8_t lastDuty = 128;
volatile uint32_t loopCount = 0;

uint32_t fileBytes = 0;
uint32_t fileHash = 2166136261u;
int16_t minSample = 32767;
int16_t maxSample = -32768;
int64_t sumAbs = 0;
uint32_t statSamples = 0;

void IRAM_ATTR onAudioTimer() {
  uint8_t duty = 128;

  portENTER_CRITICAL_ISR(&audioMux);
  if (!playbackDone && activeIndex < activeLength) {
    duty = audioData[activeIndex++];
    sampleCount++;
    if (activeIndex >= activeLength) {
      playbackDone = true;
    }
  } else if (!playbackDone) {
    underruns++;
  }
  lastDuty = duty;
  portEXIT_CRITICAL_ISR(&audioMux);

  ledcWrite(PWM_CHANNEL, duty);
}

void printPins() {
  Serial.printf("pins: amp_en_gpio%d=%d audio_gpio%d_pwm=%d input_node_gpio%d_mode=input\n",
                AMP_ENABLE_PIN, digitalRead(AMP_ENABLE_PIN), AUDIO_PIN, lastDuty,
                AMP_INPUT_NODE_PIN);
}

bool inspectAudioFile() {
  File file = LittleFS.open("/audio.s16", "r");
  if (!file) {
    Serial.println("audio: missing /audio.s16");
    return false;
  }

  fileBytes = file.size();
  if (fileBytes < 2 || (fileBytes % 2) != 0) {
    Serial.printf("audio: invalid byte count=%lu\n", fileBytes);
    file.close();
    return false;
  }

  audioData = static_cast<uint8_t *>(heap_caps_malloc(fileBytes / 2, MALLOC_CAP_8BIT));
  if (!audioData) {
    Serial.printf("audio: malloc failed bytes=%lu\n", fileBytes / 2);
    file.close();
    return false;
  }

  uint8_t bytes[256];
  uint32_t outIndex = 0;
  while (true) {
    size_t got = file.read(bytes, sizeof(bytes));
    if (!got) {
      break;
    }
    for (size_t i = 0; i < got; i++) {
      fileHash ^= bytes[i];
      fileHash *= 16777619u;
    }
    for (size_t i = 0; i + 1 < got; i += 2) {
      int16_t sample = int16_t(uint16_t(bytes[i]) | (uint16_t(bytes[i + 1]) << 8));
      minSample = min(minSample, sample);
      maxSample = max(maxSample, sample);
      sumAbs += abs(sample);
      statSamples++;
      audioData[outIndex++] = uint8_t((int(sample) + 32768) >> 8);
    }
  }
  file.close();

  Serial.printf("audio: bytes=%lu samples=%lu seconds=%.2f fnv1a=0x%08lx\n",
                fileBytes, statSamples, double(statSamples) / SAMPLE_RATE, fileHash);
  Serial.printf("audio: min=%d max=%d avg_abs=%ld\n",
                minSample, maxSample, long(statSamples ? sumAbs / statSamples : 0));
  return fileBytes >= 2 && (fileBytes % 2) == 0;
}

void startAudio() {
  pinMode(AMP_INPUT_NODE_PIN, INPUT);
  pinMode(AMP_ENABLE_PIN, OUTPUT);
  digitalWrite(AMP_ENABLE_PIN, LOW);

  double pwmResult = ledcSetup(PWM_CHANNEL, PWM_FREQ, PWM_BITS);
  ledcAttachPin(AUDIO_PIN, PWM_CHANNEL);
  ledcWrite(PWM_CHANNEL, 128);

  portENTER_CRITICAL(&audioMux);
  activeLength = statSamples;
  activeIndex = 0;
  playbackDone = statSamples == 0;
  sampleCount = 0;
  underruns = 0;
  loopCount = 0;
  portEXIT_CRITICAL(&audioMux);

  audioTimer = timerBegin(0, TIMER_DIVIDER, true);
  timerAttachInterrupt(audioTimer, &onAudioTimer, true);
  timerAlarmWrite(audioTimer, TIMER_TICKS, true);
  timerAlarmEnable(audioTimer);

  Serial.printf("playback: pwm_request=%dHz pwm_actual=%.1fHz/%dbit timer_ticks=%d actual_sample_rate=%dHz memory_samples=%lu\n",
                PWM_FREQ, pwmResult, PWM_BITS, TIMER_TICKS, ACTUAL_SAMPLE_RATE,
                statSamples);
  printPins();
}

void serviceAudio() {
  static uint32_t lastReport = 0;
  static uint32_t startMs = millis();

  if (millis() - lastReport >= 500) {
    lastReport = millis();
    Serial.printf("playback: ms=%lu samples=%lu underruns=%lu last_pwm=%u heap=%u\n",
                  millis() - startMs, sampleCount, underruns, lastDuty,
                  heap_caps_get_free_size(MALLOC_CAP_8BIT));
  }

  if (playbackDone) {
    delay(80);
    ledcWrite(PWM_CHANNEL, 128);
    loopCount++;
    Serial.printf("playback: loop=%lu samples=%lu expected=%lu underruns=%lu elapsed_ms=%lu\n",
                  loopCount, sampleCount, statSamples, underruns, millis() - startMs);
    printPins();
    delay(350);
    portENTER_CRITICAL(&audioMux);
    activeIndex = 0;
    playbackDone = false;
    sampleCount = 0;
    underruns = 0;
    portEXIT_CRITICAL(&audioMux);
    startMs = millis();
  }
}

void setup() {
  Serial.begin(115200);
  delay(1500);
  Serial.println();
  Serial.println("speaker-audio: boot");
  Serial.printf("build: %s %s\n", __DATE__, __TIME__);
  Serial.printf("heap: %u\n", heap_caps_get_free_size(MALLOC_CAP_8BIT));

  if (!LittleFS.begin(false)) {
    Serial.println("fs: LittleFS mount failed");
    return;
  }
  Serial.println("fs: LittleFS mounted");

  if (!inspectAudioFile()) {
    Serial.println("audio: invalid file, stopping");
    return;
  }

  startAudio();
}

void loop() {
  serviceAudio();
}

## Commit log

2026-04-03 ble stepper control, persist setings
2026-04-06 finish turtlebot
    [minirc1_bom.csv, minirc1_designators.csv, minirc1_positions.csv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]
2026-04-06 add schematic image
2026-04-10 test common library
    [minrc-ref.kicad_pcb, minrc-ref.kicad_sch, minrc1.kicad_sch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]
2026-05-31 stepper gui and audio
    [minrc1.kicad_pcb, minrc1.kicad_sch]
